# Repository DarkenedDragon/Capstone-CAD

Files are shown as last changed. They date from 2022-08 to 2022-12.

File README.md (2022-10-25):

# The Great Gambit &mdash; Mechanical

<!-- Buttons that link to the associated repos, uncomment all but this repo -->
<div align="center">
    The Great Gambit Logo
    <a href="https://cadlab.io/project/25988/main/files">
        CadLab Logo
    </a>
    <a href="https://github.com/TheGreatGambit/Capstone-Electrical">
        Electrical Logo - Small
    </a>
    <a href="https://github.com/TheGreatGambit/Capstone-Software">
        Software Logo - Small
    </a>
    <!-- <a href="https://github.com/TheGreatGambit/Capstone-Mechanical-CAD">
        <img src="https://github.com/TheGreatGambit/Capstone-Electrical/blob/main/Images/logo_mechanical_small.png" alt="Mechanical Logo - Small" style="height:40px;width:200px">
    </a> --!>
    <a href="https://github.com/TheGreatGambit/Capstone-PyChess">
        <img src="https://github.com/TheGreatGambit/Capstone-Electrical/blob/main/Images/logo_pychess_small.png" alt="PyChess Logo - Small" style="height:40px;width:200px">
    </a>
</div>

<!-- Brief overview of this repo -->
## Overview
This project aims to create an autonomous robot capable of playing an intelligent, over-the-board game of chess against a human opponent. The system uses a three-axis, cantilevered, overhead gantry to move parallel to the chess board. Each axis is driven by a stepper motor, the horizontal axes using belts and the vertical axis using a rack and pinion. A crosspoint array of reed switches embedded in the physical chess board allows for piece detection, and with software record of the board state, piece recognition. This system is orchestrated by an [MSP432E401Y](https://www.ti.com/product/MSP432E401Y) microcontroller, with chess moves being pulled from the open-source [Stockfish](https://github.com/official-stockfish/Stockfish) chess engine, running on a [Raspberry Pi 3A+](https://www.raspberrypi.com/products/raspberry-pi-3-model-a-plus/). All communication between the Raspberry Pi and MSP432 is done through a universal asynchronous receiver-transmitter (UART) serial connection.

This repository contains all mechanical designs for the system, generated in [Solidworks](https://www.solidworks.com/).

<!-- Any repo-specific setup, etc. -->

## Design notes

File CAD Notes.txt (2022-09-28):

- The tolerances on the lifting mechanism are way to tight (less so now)
- Is there space for a nut on the back of the arm plate?
- How to attach the magnet? - screwed into the rack? Could drill and tap the bottom of the rack and then use an M5 screw
- The lever on the limit switches is slightly smaller than the ones in the lab. I'm not sure if the body is different, but the positioning should remain the same
- Need to think about cable management. Could probably put a cable carrier on the top of the arm. Couldn't model it without straining my computer
- The motor mounting plate on the arm may be replaced with the one in the lab. It's larger and thus has more space for adding counterweights
- The piece lifiting mechanisim isn't very compliant
- Manufacturing the rack could be hard. I was thinking we'd need to mill out the channels, but I need to talk to the people in Lacy to see if that's doable. 
- I modeled an Openbuilds Nema 17 stepper for the lifter, but I found a smaller form factor on Sparkfun (https://www.sparkfun.com/products/9238)
- The smaller stepper is in the Lifting-Mechansim-Stepper-Small assembly
- I'd like to prototype the mount for the lifter. Would require ordering the rack and pinion from McMaster
- I am assuming there is some sort of collar on the pinon, and it's just not modeled for simplistiy. I don't see any other way of doing the power transfer
- The smaller stepper has a holding torque of 0.23 Nm according to its datasheet (https://www.sparkfun.com/datasheets/Robotics/SM-42BYG011-25.pdf), 
which means 0.23 NM = F x 10mm => F = 2.3N. That's about 0.5 lbs. 
- Openbuilds says the larger stepper has 76 oz*in of holding torque or about 0.5 Nm. That's enough to support 5N or 1.1 lbs. That should be enough? 
I'm not sure how much the magnet + rack would weigh. This is at 24 volts
- Linear stepper motors are WAY too expensive, and lead screws need a lot of extra support
- The rack is long enough for both pawns and the king

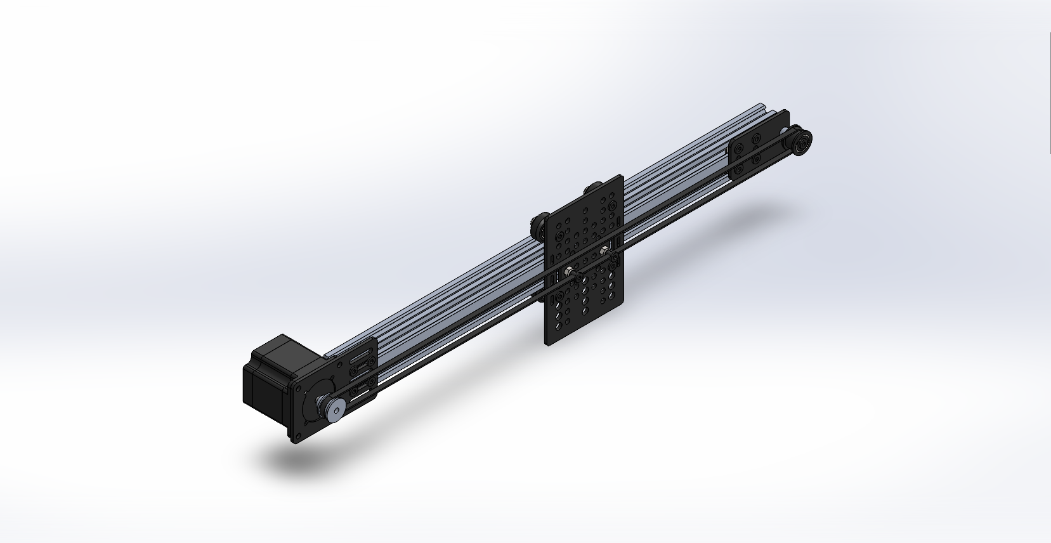
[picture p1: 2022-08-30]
Images/Gantry-System-V1.png

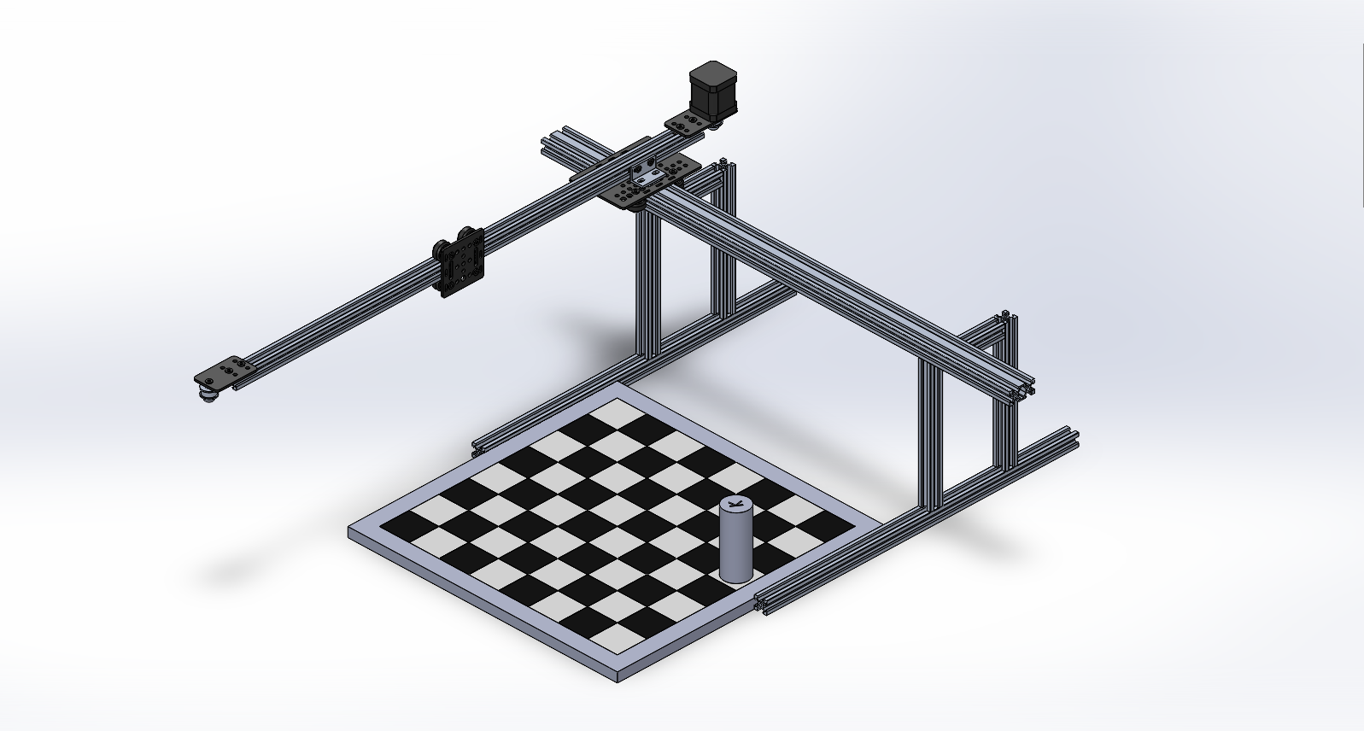
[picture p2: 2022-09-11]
Images/Gantry-System-V3.png

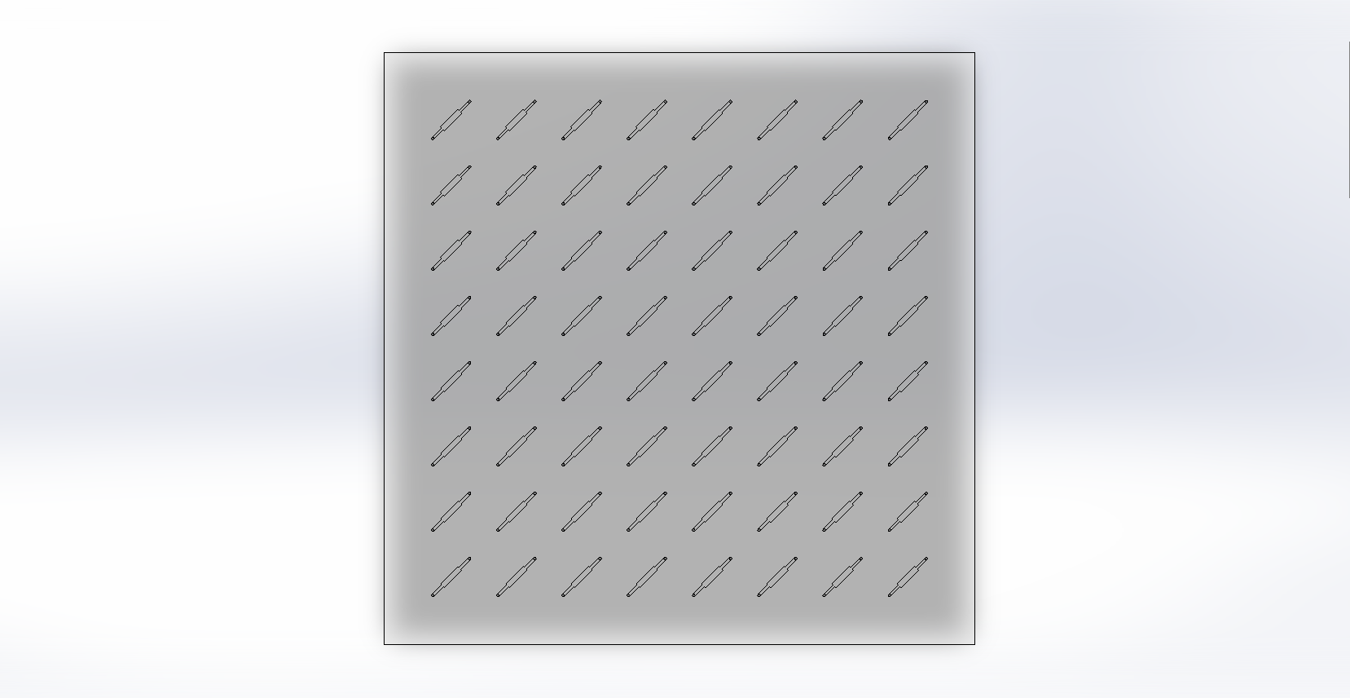
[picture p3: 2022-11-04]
Images/reed_switch_array_v2_overhead.png

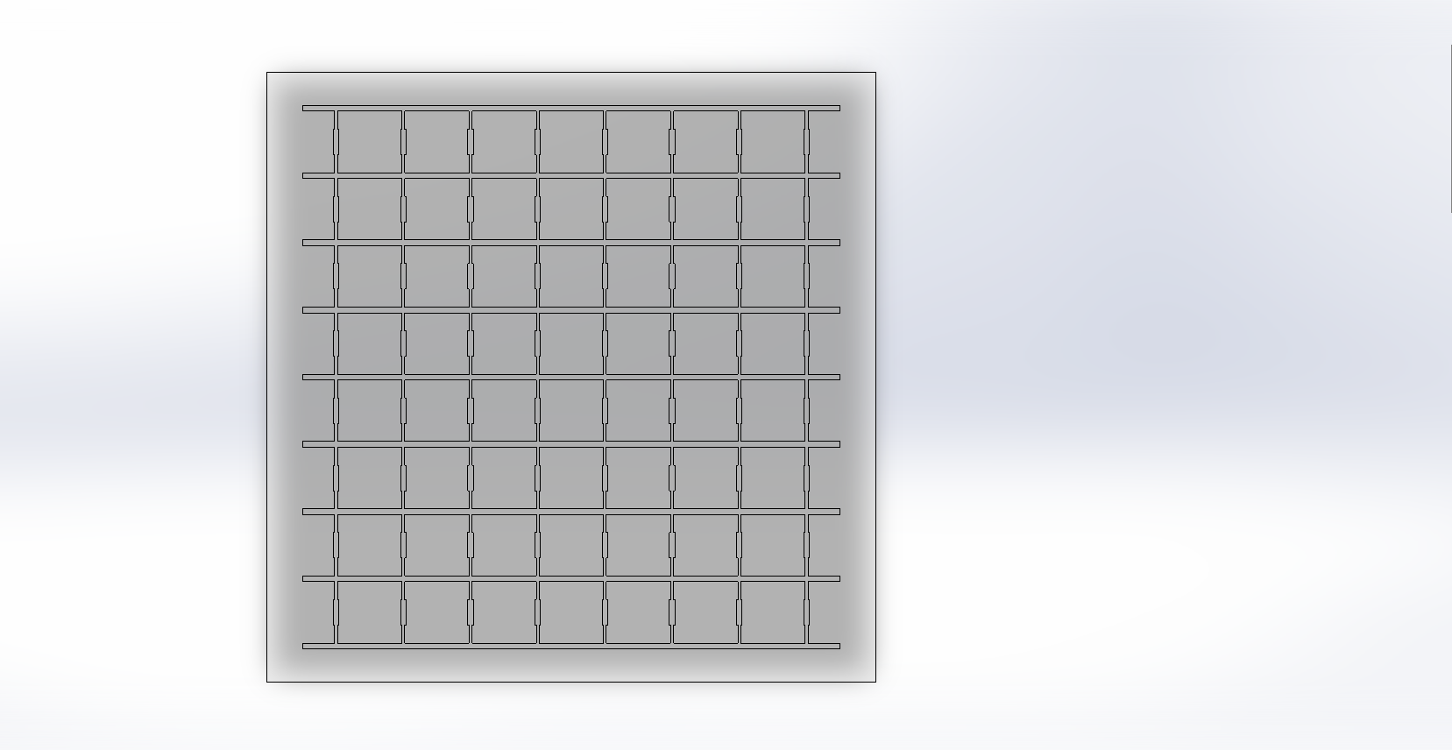
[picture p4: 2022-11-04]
Images/reed_switch_array_v1_overhead.png

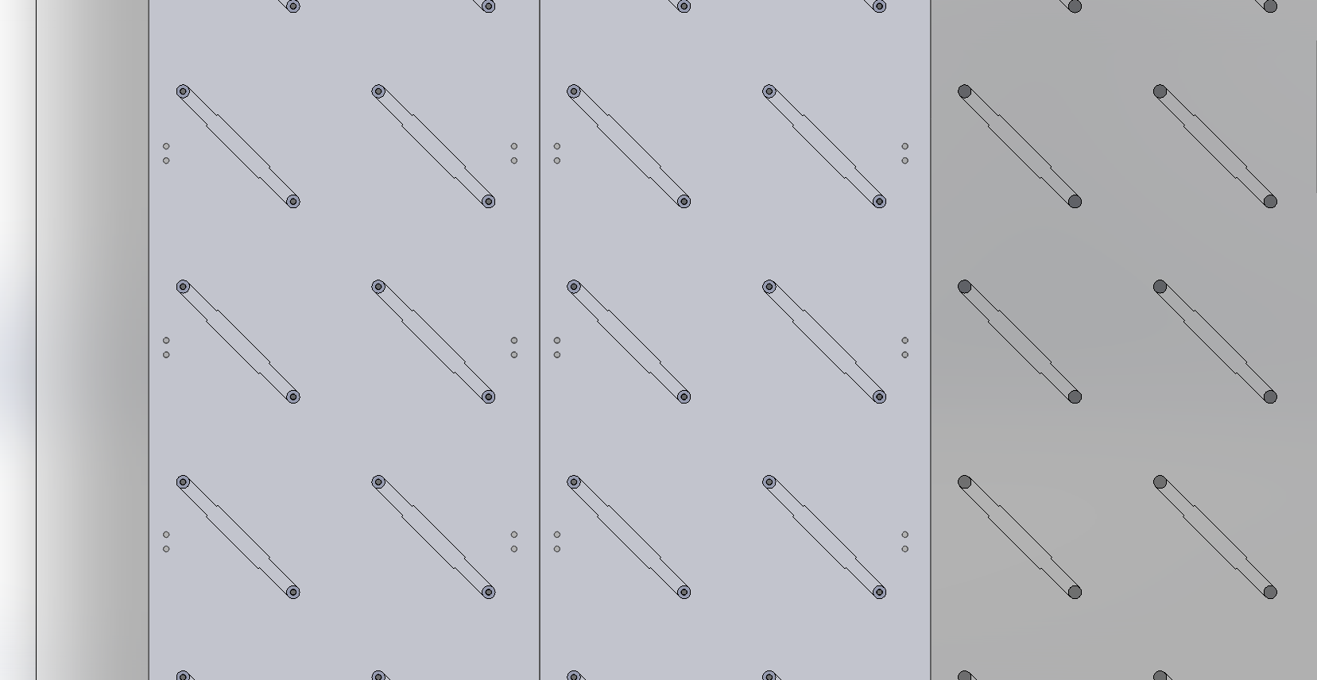
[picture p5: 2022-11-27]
Images/reed_switch_board_v2.png

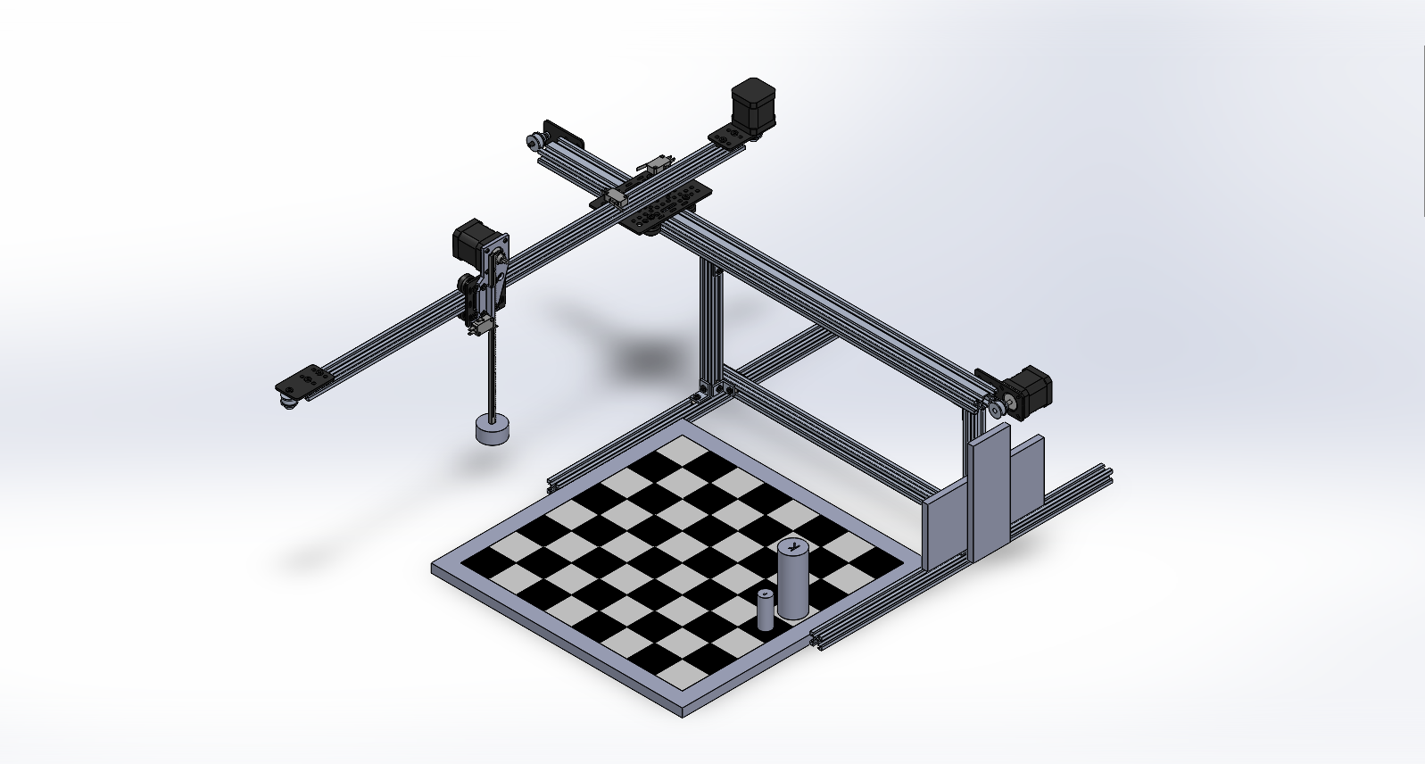
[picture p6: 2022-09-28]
Images/Gantry-System-V6.png

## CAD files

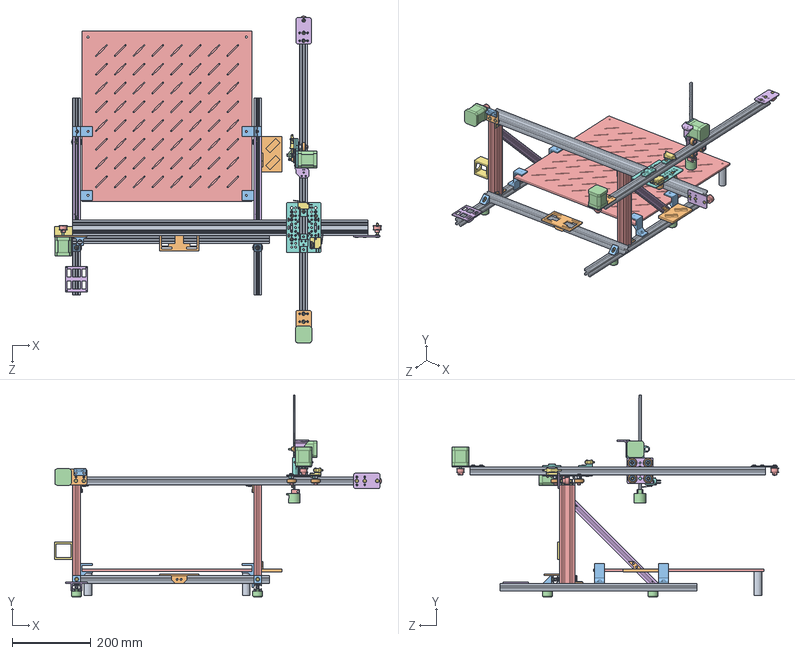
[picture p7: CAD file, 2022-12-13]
Gantry System/TheGreatGambit.SLDASM
830.2 x 512.0 x 829.4 mm
V-Slot 20x20x1000 Linear Rail
Solid V Wheel x 8
Ball Bearing 5 x 16 x 5 x 16
Precision Shim 10 x 5 x 1 x 12
Nylon Insert Lock Nut M5 x 8
V-Slot Gantry Plate 20mm
Low Profile Screw M5 x 54
Eccentric Spacer 6mm x 6
Aluminum Spacer 6mm x 6
Motor Mount Plate Nema 17 x 2
Double Tee Nut x 6
Nema 17 Stepper Motor x 3
GT3 Timing Pulley 20 Tooth x 4
Idler Pulley Plate x 2
Aluminum Spacer 3mm x 2
V-Slot Gantry Plate 20-80mm
V-Slot 20x20x500 Linear Rail x 3
L Bracket Single x 8
Black Angle Corner Connector x 2
Tee Nut x 24
V-Slot 20x40x250 Linear Rail x 2
V-Slot 20x20x300 Corner Linear Rail x 2
7779K530_MINIATURE SNAP-ACTING SWITCH x 3
Lifting-Mechanism-Stepper-Mount-Plate
2662N56_20 Degree Pressure Angle Gear Rack
2662N33_20 Degree Pressure Angle Plastic Gear
Button Head Socket Cap Screw M3 x 4
electromagnet_holder
electromagnet_holder_clip
z_cable_carrier_holder
Limit-Switch-Mount-Gantry-Plate
Limit-Switch-Mount-V-Slot-Rail
V-Slot 20x40x750 Linear Rail
MSP-Mount
board_support x 4
3136N147_T-Slotted Framing x 4
reed_switch_holder
pi_holder
e_stop_mount
cable_carrier_rail
board_middle_support x 2
spare_queen_holder
signal_light_holder

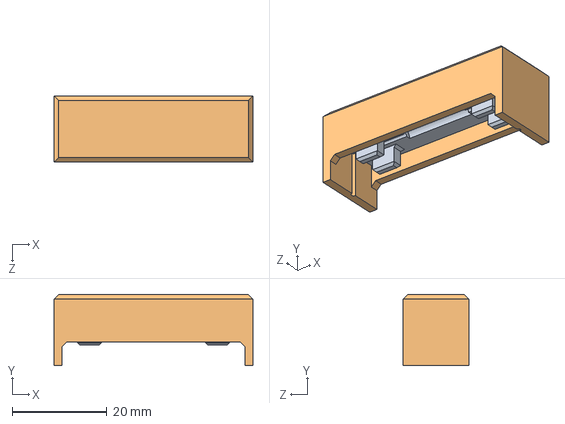
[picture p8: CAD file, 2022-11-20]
Reed Switch Bender/reed_switch_bender.SLDASM
42.0 x 15.0 x 14.0 mm
reed_switch_bender_top
reed_switch_bender_lid

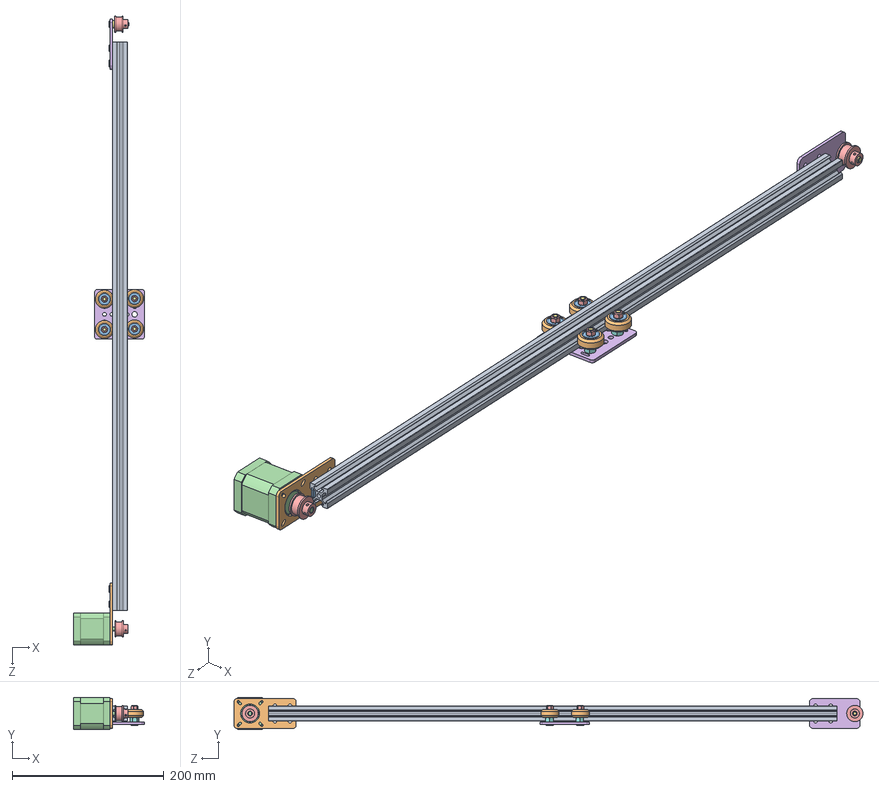
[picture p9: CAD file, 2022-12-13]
Gantry System/gantry-arm.SLDASM
93.3 x 42.4 x 829.4 mm
V-Slot 20x20x1000 Linear Rail
Solid V Wheel x 4
Ball Bearing 5 x 16 x 5 x 8
Precision Shim 10 x 5 x 1 x 4
Nylon Insert Lock Nut M5 x 4
V-Slot Gantry Plate 20mm
Low Profile Screw M5 x 9
Eccentric Spacer 6mm x 2
Aluminum Spacer 6mm x 2
Motor Mount Plate Nema 17
Double Tee Nut x 2
Nema 17 Stepper Motor
GT3 Timing Pulley 20 Tooth x 2
Idler Pulley Plate
Aluminum Spacer 3mm

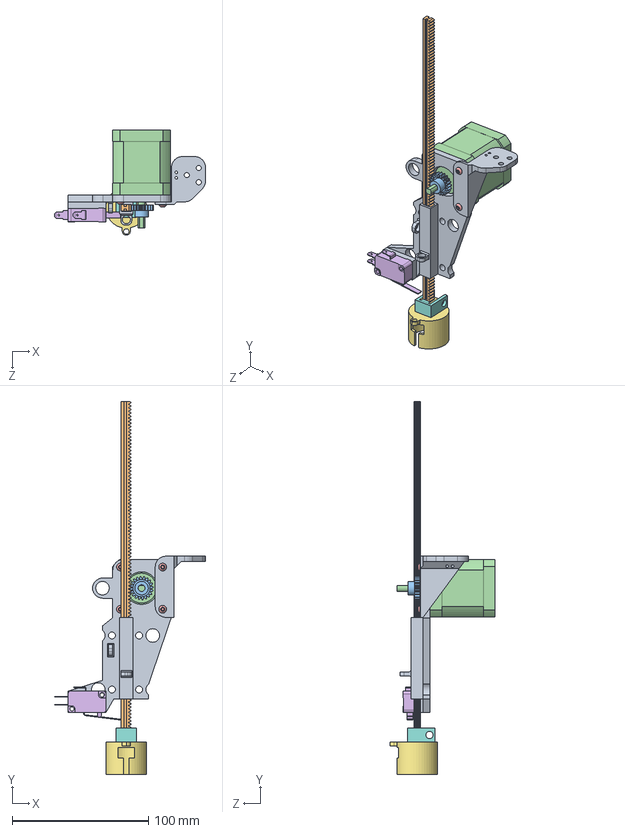
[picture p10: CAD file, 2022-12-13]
Gantry System/Lifting-Mechanism-Stepper.SLDASM
111.0 x 274.0 x 77.5 mm
Lifting-Mechanism-Stepper-Mount-Plate
2662N56_20 Degree Pressure Angle Gear Rack
2662N33_20 Degree Pressure Angle Plastic Gear
Nema 17 Stepper Motor
Button Head Socket Cap Screw M3 x 4
7779K530_MINIATURE SNAP-ACTING SWITCH
electromagnet_holder
electromagnet_holder_clip
z_cable_carrier_holder

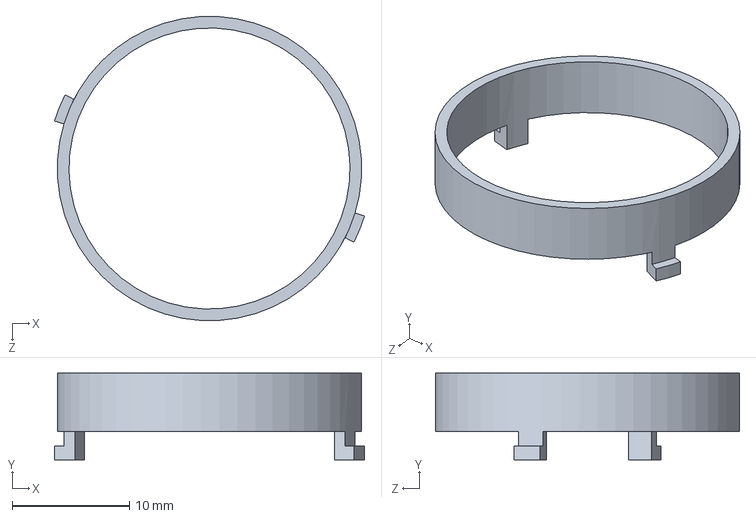
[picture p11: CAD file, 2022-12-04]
Gantry System/interlocking.SLDASM
26.5 x 7.40 x 26.0 mm

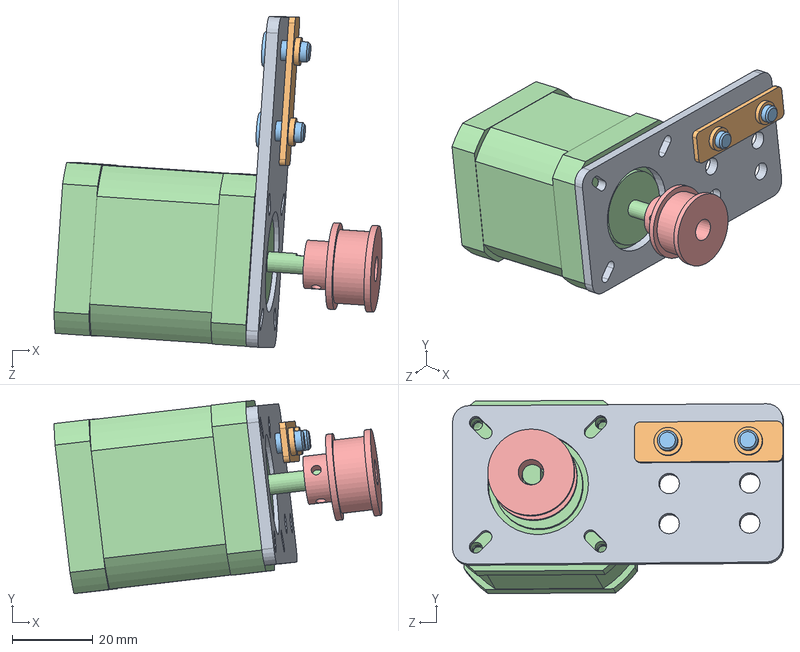
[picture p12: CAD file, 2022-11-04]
Gantry System/Nema 17 Stepper Mount 20x40.SLDASM
81.3 x 47.9 x 82.1 mm
Motor Mount Plate Nema 17
Double Tee Nut
Low Profile Screw M5 x 2
Nema 17 Stepper Motor
GT3 Timing Pulley 20 Tooth

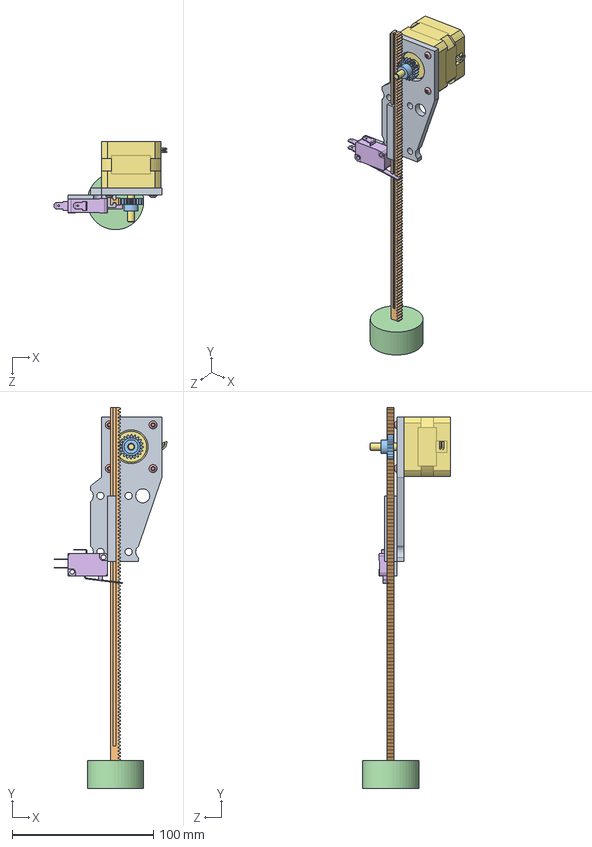
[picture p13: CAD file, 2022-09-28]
Gantry System/Lifting-Mechanism-Stepper-Small.SLDASM
79.9 x 270.0 x 62.5 mm
Lifting-Mechanism-Stepper-Mount-Plate
2662N56_20 Degree Pressure Angle Gear Rack
2662N33_20 Degree Pressure Angle Plastic Gear
ElectroMagnet-Model
Button Head Socket Cap Screw M3 x 4
7779K530_MINIATURE SNAP-ACTING SWITCH

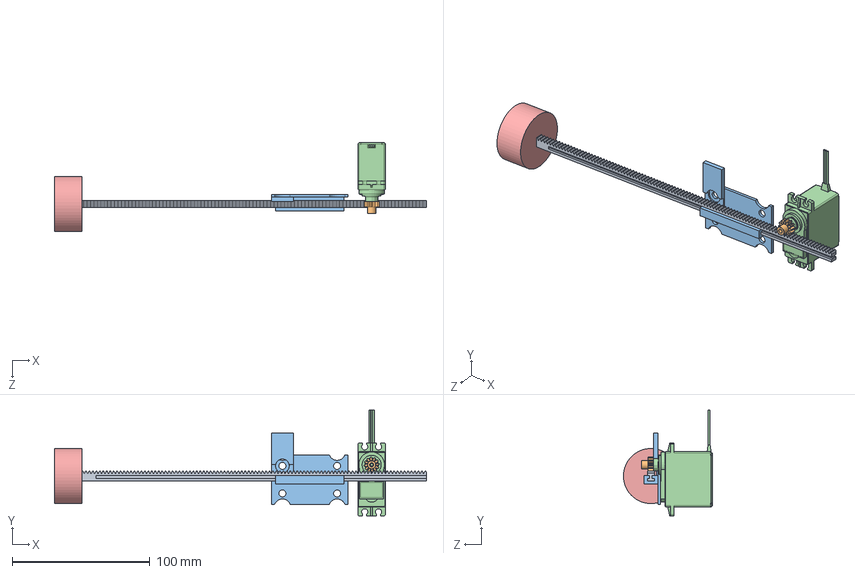
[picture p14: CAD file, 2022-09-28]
Gantry System/Piece-Lifting-Mechanism.SLDASM
270.0 x 76.8 x 64.7 mm
2662N56_20 Degree Pressure Angle Gear Rack
2662N322_20 Degree Pressure Angle Plastic Gear
Rack-Holder
HS-5485HB Servo
ElectroMagnet-Model

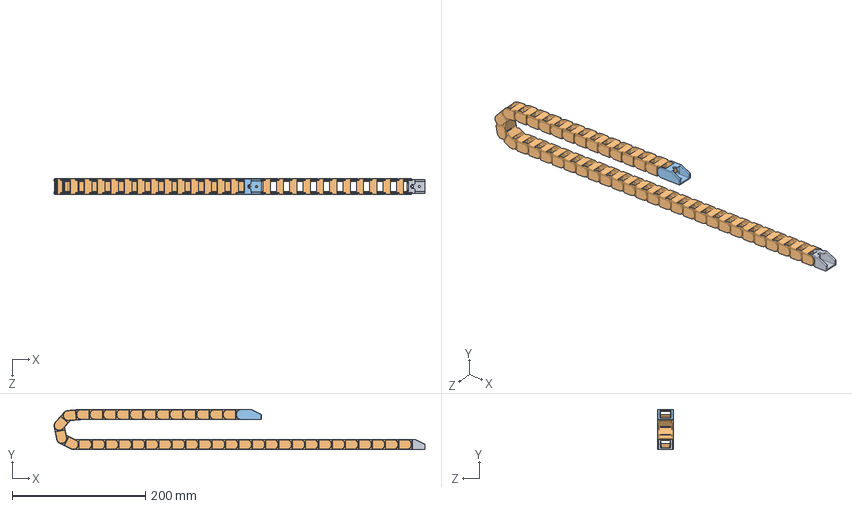
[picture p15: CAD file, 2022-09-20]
Gantry System/X-Carrage Chain Assebmly.SLDPRT.SLDASM
556.8 x 60.5 x 23.9 mm
Drag Chain 10x15 M-End
Drag Chain 10x15 Inner x 41
Drag Chain 10x15 F-End

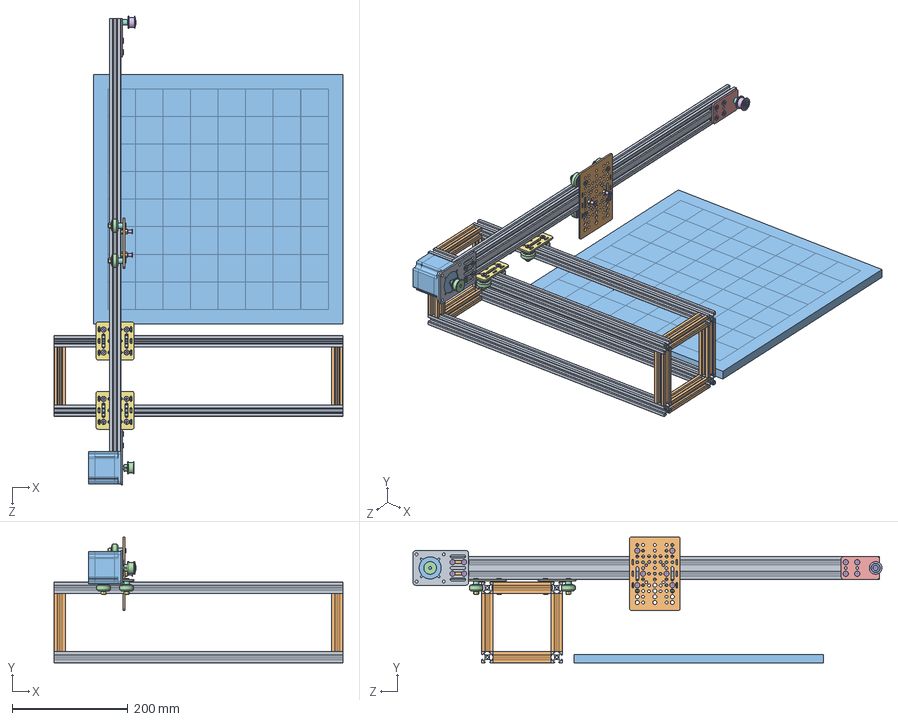
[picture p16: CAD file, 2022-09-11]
Gantry System/Gantry-System-V1.SLDASM
500.0 x 218.0 x 811.9 mm
V-Slot 20x40x500 Linear Rail
V-Slot Gantry Plate 20-80mm
Ball Bearing 5 x 16 x 5 x 26
Solid V Wheel x 12
Precision Shim 10 x 5 x 1 x 12
Low Profile Screw M5 x 27
Nylon Insert Lock Nut M5 x 17
Aluminum Spacer 9mm x 5
Motor Mount Plate Nema 23
Double Tee Nut x 6
Nema 23 Stepper Motor
GT2 Timing Pulley 30 Tooth
Idler Pulley Plate
Smooth Idler Pulley Wheel
V-Slot Gantry Plate 20mm x 2
Aluminum Spacer 6mm x 8
V-Slot 20x20x500 Linear Rail x 4
V-Slot 20x20x100 Linear Rail x 8
chess_board

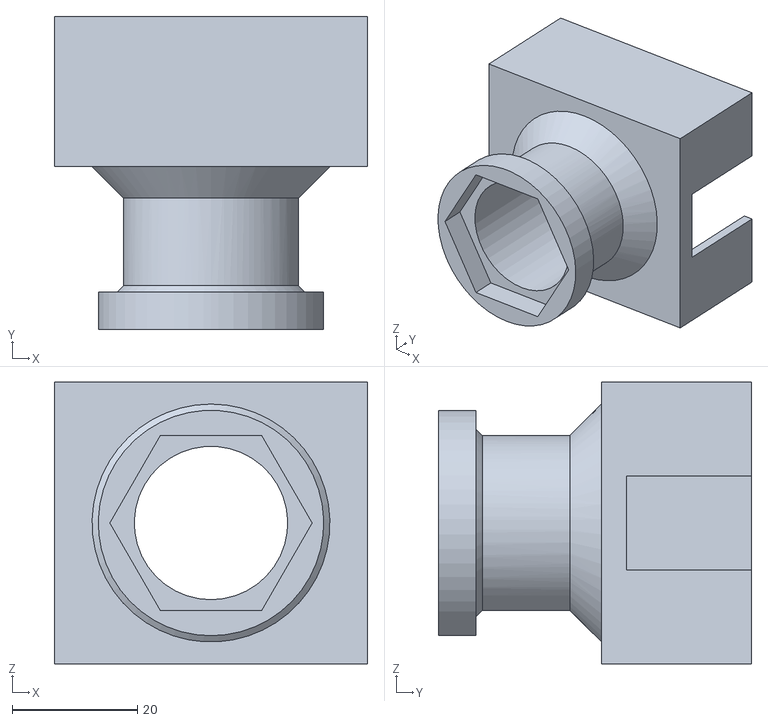
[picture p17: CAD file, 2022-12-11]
Gantry System/STL files/next_turn_btn_holder_v3.STL
50.0 x 50.0 x 45.0

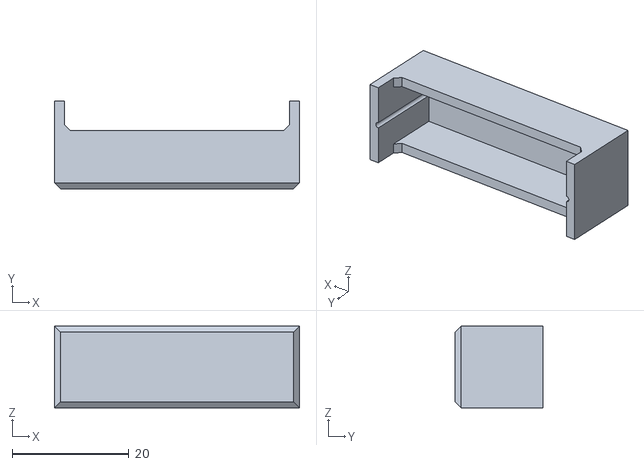
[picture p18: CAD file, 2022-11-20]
Reed Switch Bender/STL Files/reed_switch_bender_lid_v1.STL
42.0 x 15.0 x 14.0

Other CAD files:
Gantry System/Idle Pulley Mount 20x40.SLDASM
Gantry System/Idle Pulley Mount.SLDASM
Gantry System/Nema 17 Stepper Mount.SLDASM
Gantry System/V-Slot 20x40 Cart.SLDASM
Gantry System/Gantry-Arm-Bracket-Mount.SLDASM
Gantry System/V-Slot 20x20 Cart.SLDASM
Gantry System/2662N23_20 Degree Pressure Angle Plastic Gear.SLDPRT
Gantry System/2662N322_20 Degree Pressure Angle Plastic Gear.SLDPRT
Gantry System/2662N325_20 Degree Pressure Angle Plastic Gear.SLDPRT
Gantry System/2662N33_20 Degree Pressure Angle Plastic Gear.SLDPRT
Gantry System/2662N56_20 Degree Pressure Angle Gear Rack.SLDPRT
Gantry System/3136N147_T-Slotted Framing.SLDPRT
Gantry System/47065T736_Silver Gusset Bracket.SLDPRT
Gantry System/5537T658_T-Slotted Framing.SLDPRT
Gantry System/5537T69_T-Slotted Framing.SLDPRT
Gantry System/6812N44_T-Slotted Framing.SLDPRT
Gantry System/7779K530_MINIATURE SNAP-ACTING SWITCH.SLDPRT
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

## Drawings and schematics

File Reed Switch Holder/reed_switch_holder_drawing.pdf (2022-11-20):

6

5

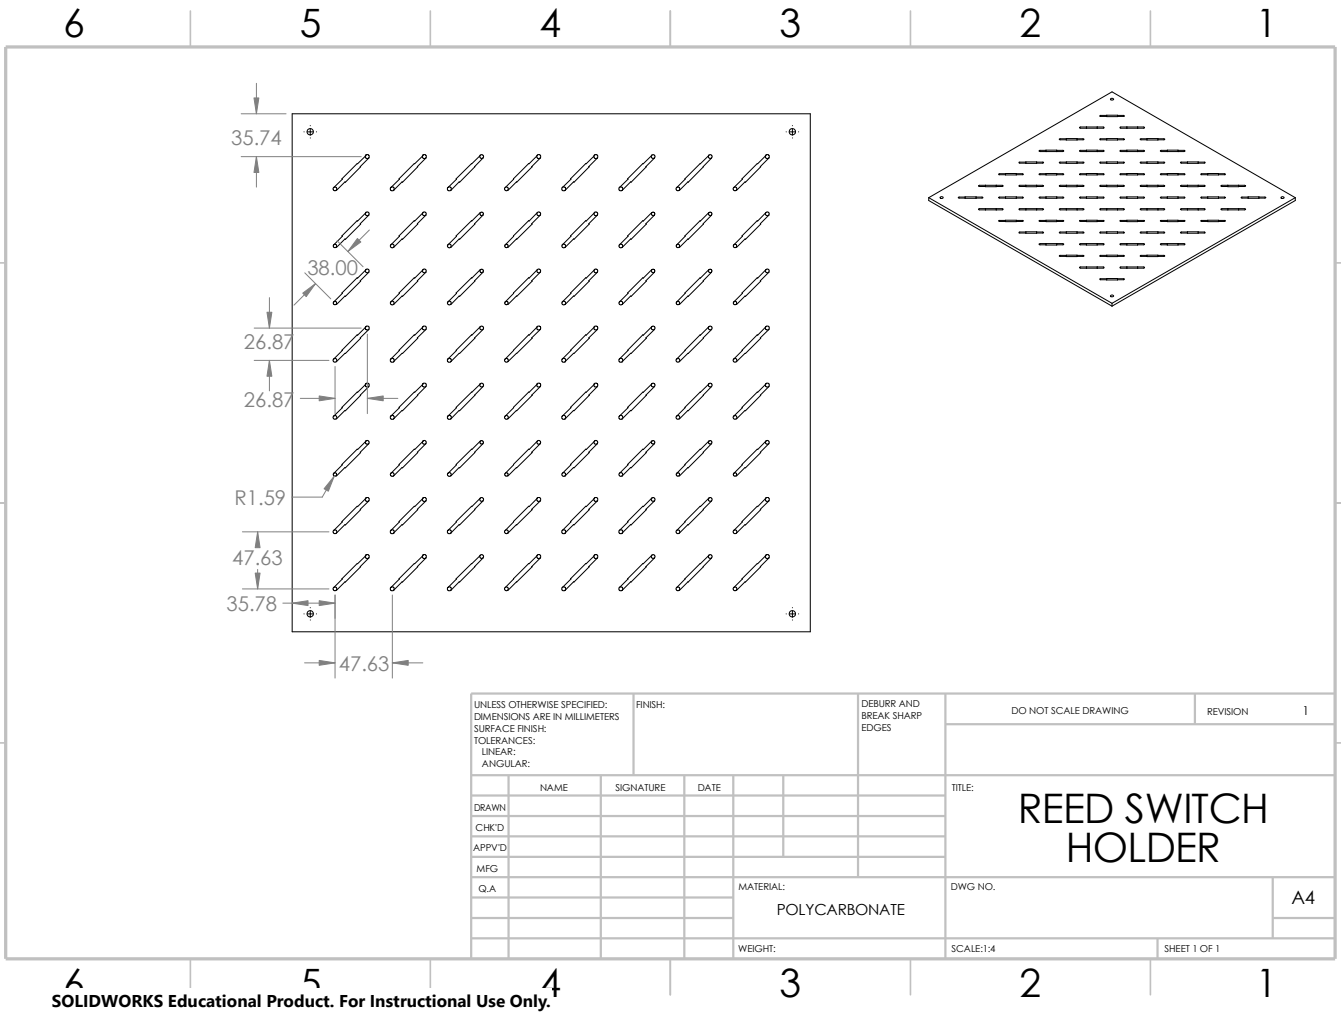
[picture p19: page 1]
BREAK SHARP; WEIGHT:; SHEET 1 OF 1; SCALE:1:4; FINISH:; EDGES; DO NOT SCALE DRAWING; REVISION; DEBURR AND

UNLESS OTHERWISE SPECIFIED:
DIMENSIONS ARE IN MILLIMETERS
SURFACE FINISH:
TOLERANCES:
LINEAR:
ANGULAR:

NAME | SIGNATURE | DATE | | | | TITLE: REED SWITCH HOLDER

DRAWN
CHK'D
APPV'D

MFG
Q.A | | | | MATERIAL: POLYCARBONATE | DWG NO. | A4

SOLIDWORKS Educational Product. For Instructional Use Only.

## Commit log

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2022-09-10 Added new sub assemblies Signed-off-by: Eli Jelesko <eridor314@gmail.com>
    [Gantry-System-V1.SLDASM, Idle Pulley Mount.SLDASM, Nema 17 Stepper Mount.SLDASM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]
2022-09-19 Added brackets to the frame
    [Gantry-Arm-Bracket-Mount.SLDASM, Idle Pulley Mount.SLDASM, Nema 17 Stepper Mount.SLDASM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]
2022-09-19 Adjusted the arms mounting
    [TheGreatGambit.SLDASM]
2022-09-19 Added initial parts for the lifting mechanism
    [2662N23_20 Degree Pressure Angle Plastic Gear.SLDPRT, 2662N56_20 Degree Pressure Angle Gear Rack.SLDPRT, ElectroMagnet-Model.SLDPRT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]
2022-09-20 Adjusted motor mounting for the 2nd axis
    [2662N322_20 Degree Pressure Angle Plastic Gear.SLDPRT, 2662N56_20 Degree Pressure Angle Gear Rack.SLDPRT, HS-5485HB Servo.SLDPRT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]
2022-09-20 Added the motor mounts for the 2d axis
    [Idle Pulley Mount 20x40.SLDASM, TheGreatGambit.SLDASM]
2022-09-20 Updated the rack holder part to suppor the servo
    [2662N322_20 Degree Pressure Angle Plastic Gear.SLDPRT, 2662N56_20 Degree Pressure Angle Gear Rack.SLDPRT, Piece-Lifting-Mechanism.SLDASM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]
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2022-09-20 Updates. Tried adding cable carrier. Removed due to performance
    [2662N56_20 Degree Pressure Angle Gear Rack.SLDPRT, PCB-Model.SLDPRT, Piece-Lifting-Mechanism.SLDASM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]
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2022-09-20 Put the slit in the rack back
    [2662N56_20 Degree Pressure Angle Gear Rack.SLDPRT, Piece-Lifting-Mechanism.SLDASM, TheGreatGambit.SLDASM]
2022-09-27 Realigned to origin planes
    [TheGreatGambit.SLDASM]
2022-09-27 Fixed overconstrianed issues
    [Piece-Lifting-Mechanism.SLDASM, TheGreatGambit.SLDASM, gantry-arm.SLDASM]
2022-09-28 Added assembly using smaller stepper motor
    [9238.sldprt, Lifting-Mechanism-Stepper-Small.SLDASM, TheGreatGambit.SLDASM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]
2022-09-28 Mated to origin planes
    [Lifting-Mechanism-Stepper-Small.SLDASM, Lifting-Mechanism-Stepper.SLDASM]
2022-09-29 Transparent image for poster
    [TheGreatGambit.SLDASM]
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2022-10-04 Added limit switch plates and adjusted the lifting mount
    [Idle Pulley Mount 20x40.SLDASM, Idle Pulley Mount.SLDASM, Lifting-Mechanism-Stepper-Mount-Plate-V2.STL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]
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2022-10-10 Adjusted limit switch mounts
    [3136N147_T-Slotted Framing.SLDPRT, 6812N44_T-Slotted Framing.SLDPRT, Limit-Switch-Mount-Gantry-Plate-V2.STL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]
2022-10-25 Created a mount for the MSP and adjusted the limit switch mount
    [Idle Pulley Mount 20x40.SLDASM, Idle Pulley Mount.SLDASM, Limit-Switch-Mount-Gantry-Plate.SLDPRT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]
2022-11-04 reed switch array v1
    [Idle Pulley Mount 20x40.SLDASM, Idle Pulley Mount.SLDASM, MSP-Mount.STL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]
2022-11-04 Reed switch layout v2
    [reed_switch_holder.SLDPRT]
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2022-11-08 Added electromagnet holder and added cable managment features
    [Lifting-Mechanism-Stepper-Mount-Plate-V3.STL, Lifting-Mechanism-Stepper-Mount-Plate.SLDPRT, Lifting-Mechanism-Stepper.SLDASM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]
2022-11-14 Updated z mounting plate and emag holder
    [Lifting-Mechanism-Stepper-Mount-Plate-V4.STL, Lifting-Mechanism-Stepper-Mount-Plate.SLDPRT, electromagnet_holder.SLDPRT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]
2022-11-15 Added limit switch plate STL
    [Lifting-Mechanism-Stepper.SLDASM, Limit-Switch-Mount-Gantry-Plate-V3.STL]
2022-11-20 Redid the file structure and added a reed switch holder drawing
    [2662N23_20 Degree Pressure Angle Plastic Gear.SLDPRT, 2662N322_20 Degree Pressure Angle Plastic Gear.SLDPRT, 2662N325_20 Degree Pressure Angle Plastic Gear.SLD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]
2022-11-20 Added reed switch bender
    [reed_switch_bender.SLDASM, reed_switch_bender_base.SLDPRT, reed_switch_bender_base_v1.STL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]
2022-11-21 Updated z mounting plate, electromag holder, and added cable carrier mounts
    [Lifting-Mechanism-Stepper-Mount-Plate-V5.STL, Lifting-Mechanism-Stepper-Mount-Plate.SLDPRT, Sensor_Board_2x16.SLDASM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]
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2022-11-22 Updated z cable carrier and electromagent holders
    [electromagnet_holder.SLDPRT, electromagnet_holder_v4.STL, z_cable_carrier_holder.SLDPRT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]
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2022-11-27 Added next turn button holder test
    [MSP-Mount_v1.STL, UI_stand.SLDPRT, next_turn_btn_holder_v1.STL]
2022-11-27 Added first iteration of the board supports
    [Lifting-Mechanism-Stepper.SLDASM, TheGreatGambit.SLDASM, board_support.SLDPRT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]
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2022-12-04 Added capture tile and interlocking test
    [Capture_tile.SLDPRT, Capture_tile_v1.STL, UI_stand.SLDPRT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]
2022-12-05 Added signal light holder
    [board_support.SLDPRT, board_support_v2.STL, signal_light_holder.SLDPRT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]
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2022-12-09 Added e-stop mount and adjusted board support and gpio_cover
    [board_support.SLDPRT, board_support_v3.STL, e_stop_mount.SLDPRT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]
2022-12-09 Adjusted the piece bases
    [Major_piece_base.SLDPRT, Major_piece_base_v2.STL, Pawn_piece_base.SLDPRT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]
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2022-12-09 Updated piece bases and the queen holder
    [Major_piece_base.SLDPRT, Major_piece_base_v3.STL, Pawn_piece_base.SLDPRT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]
2022-12-09 Shortened the board holder
    [Pawn_piece_base.SLDPRT, board_support.SLDPRT, board_support_v4.STL]
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2022-12-10 Updated spare queen holder
    [spare_queen_holder.SLDPRT, spare_queen_holder_v3.STL]
2022-12-10 Shifted the spare queen orientation
    [spare_queen_holder.SLDPRT, spare_queen_holder_v4.STL]
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2022-12-11 Updated the next turn holder and the e-mag clip
    [UI_stand.SLDPRT, electromagnet_holder_clip.SLDPRT, electromagnet_holder_clip_v2.STL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]
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
